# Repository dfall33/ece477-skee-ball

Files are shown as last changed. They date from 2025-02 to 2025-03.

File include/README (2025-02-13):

This directory is intended for project header files.

A header file is a file containing C declarations and macro definitions
to be shared between several project source files. You request the use of a
header file in your project source file (C, C++, etc) located in `src` folder
by including it, with the C preprocessing directive `#include'.

```src/main.c

#include "header.h"

int main (void)
{
 ...
}
```

Including a header file produces the same results as copying the header file
into each source file that needs it. Such copying would be time-consuming
and error-prone. With a header file, the related declarations appear
in only one place. If they need to be changed, they can be changed in one
place, and programs that include the header file will automatically use the
new version when next recompiled. The header file eliminates the labor of
finding and changing all the copies as well as the risk that a failure to
find one copy will result in inconsistencies within a program.

In C, the usual convention is to give header files names that end with `.h'.
It is most portable to use only letters, digits, dashes, and underscores in
header file names, and at most one dot.

Read more about using header files in official GCC documentation:

* Include Syntax
* Include Operation
* Once-Only Headers
* Computed Includes

https://gcc.gnu.org/onlinedocs/cpp/Header-Files.html

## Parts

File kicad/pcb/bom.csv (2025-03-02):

Reference | Value | Datasheet | Footprint | Qty | DNP
C1 | 10nF | ~ | Capacitor_SMD:C_0805_2012Metric_Pad1.18x1.45mm_HandSolder | 1
C3,C6,C10,C12,C14,C16 | 100nF | ~ | Capacitor_SMD:C_0805_2012Metric_Pad1.18x1.45mm_HandSolder | 6
C2 | 1uF | ~ | Capacitor_SMD:C_0805_2012Metric_Pad1.18x1.45mm_HandSolder | 1
C11,C17 | 4.7uF | ~ | Capacitor_SMD:C_0805_2012Metric_Pad1.18x1.45mm_HandSolder | 2
C7 | 10uF | ~ | Capacitor_SMD:C_0805_2012Metric_Pad1.18x1.45mm_HandSolder | 1
R3,R4,R5,R6,R7,R8,R11 | 150 | ~ | Resistor_SMD:R_0805_2012Metric_Pad1.20x1.40mm_HandSolder | 7
R9 | 200 | ~ | Resistor_SMD:R_0805_2012Metric_Pad1.20x1.40mm_HandSolder | 1
R10 | 300 | ~ | Resistor_SMD:R_0805_2012Metric_Pad1.20x1.40mm_HandSolder | 1
R1,R2 | 10k | ~ | Resistor_SMD:R_0805_2012Metric_Pad1.20x1.40mm_HandSolder | 2
RV1 | 10k | ~ | Potentiometer_THT:Potentiometer_Bourns_3339P_Vertical | 1
U5,U6 | 74HC595 | http://www.ti.com/lit/ds/symlink/sn74hc595.pdf | 74HC595N:SOT38-4_NXP | 2
U7 | 74LS08 | http://www.ti.com/lit/gpn/sn74LS08 | SN74LS08N:N14 | 1
J4 | Barrel_Jack | ~ | Connector_BarrelJack:BarrelJack_CUI_PJ-063AH_Horizontal | 1
J5 | Conn_01x05 | ~ | Connector_PinHeader_2.54mm:PinHeader_1x05_P2.54mm_Vertical | 1
J3 | Conn_02x06_Counter_Clockwise | ~ | Connector_PinHeader_2.54mm:PinHeader_2x06_P2.54mm_Vertical | 1
U3 | D24V22F5 | https://engineering.purdue.edu/477grp1/Files/refs/d24v22f5.pdf | 12V_2.2A_STEP-DOWN_D24V22F12:XDCR_12V_2.2A_STEP-DOWN_D24V22F12 | 1
U1 | D24V22F6 | https://engineering.purdue.edu/477grp1/Files/refs/d24v22f6.pdf | 12V_2.2A_STEP-DOWN_D24V22F12:XDCR_12V_2.2A_STEP-DOWN_D24V22F12 | 1
J18 | DC_DRIVER | ~ | Connector_PinHeader_2.54mm:PinHeader_1x02_P2.54mm_Vertical | 1
J2 | EXTERNAL_BUTTON | ~ | Connector_PinHeader_2.54mm:PinHeader_1x02_P2.54mm_Vertical | 1
FB1 | FerriteBead | ~ | Capacitor_SMD:C_0805_2012Metric_Pad1.18x1.45mm_HandSolder | 1
J13 | HEADER | ~ | Connector_PinHeader_2.54mm:PinHeader_1x03_P2.54mm_Vertical | 1
J19 | JOYSTICK | ~ | Connector_PinHeader_2.54mm:PinHeader_1x03_P2.54mm_Vertical | 1
U13 | LD1117S33TR_SOT223 | http://www.st.com/st-web-ui/static/active/en/resource/technical/document/datasheet/CD00000544.pdf | Package_TO_SOT_SMD:SOT-223-3_TabPin2 | 1
D1,D2,D3,D4,D5,D6,D7,D8,D9 | LED | ~ | LED_SMD:LED_0805_2012Metric_Pad1.15x1.40mm_HandSolder | 9
U2 | MAX98357A | https://www.analog.com/media/en/technical-documentation/data-sheets/MAX98357A-MAX98357B.pdf | max98357A:MAX98347A_ADAFRUIT_I2S_BREAKOUT | 1
J20 | SERVO | ~ | Connector_PinHeader_2.54mm:PinHeader_1x03_P2.54mm_Vertical | 1
U4 | STM32F091RCTx | https://engineering.purdue.edu/477grp1/Files/refs/stm32f091cc.pdf | Package_QFP:LQFP-64_10x10mm_P0.5mm | 1
SW1 | SW_Push | ~ | Button_Switch_THT:SW_PUSH_6mm | 1
J21 | US0 | ~ | Connector_PinHeader_2.54mm:PinHeader_1x04_P2.54mm_Vertical | 1
J22 | US1 | ~ | Connector_PinHeader_2.54mm:PinHeader_1x04_P2.54mm_Vertical | 1
J26 | US2 | ~ | Connector_PinHeader_2.54mm:PinHeader_1x04_P2.54mm_Vertical | 1
J27 | US3 | ~ | Connector_PinHeader_2.54mm:PinHeader_1x04_P2.54mm_Vertical | 1
J36 | US4 | ~ | Connector_PinHeader_2.54mm:PinHeader_1x04_P2.54mm_Vertical | 1
U8,U9,U10 | ~ |  | Package_DIP:DIP-12_W10.16mm | 3

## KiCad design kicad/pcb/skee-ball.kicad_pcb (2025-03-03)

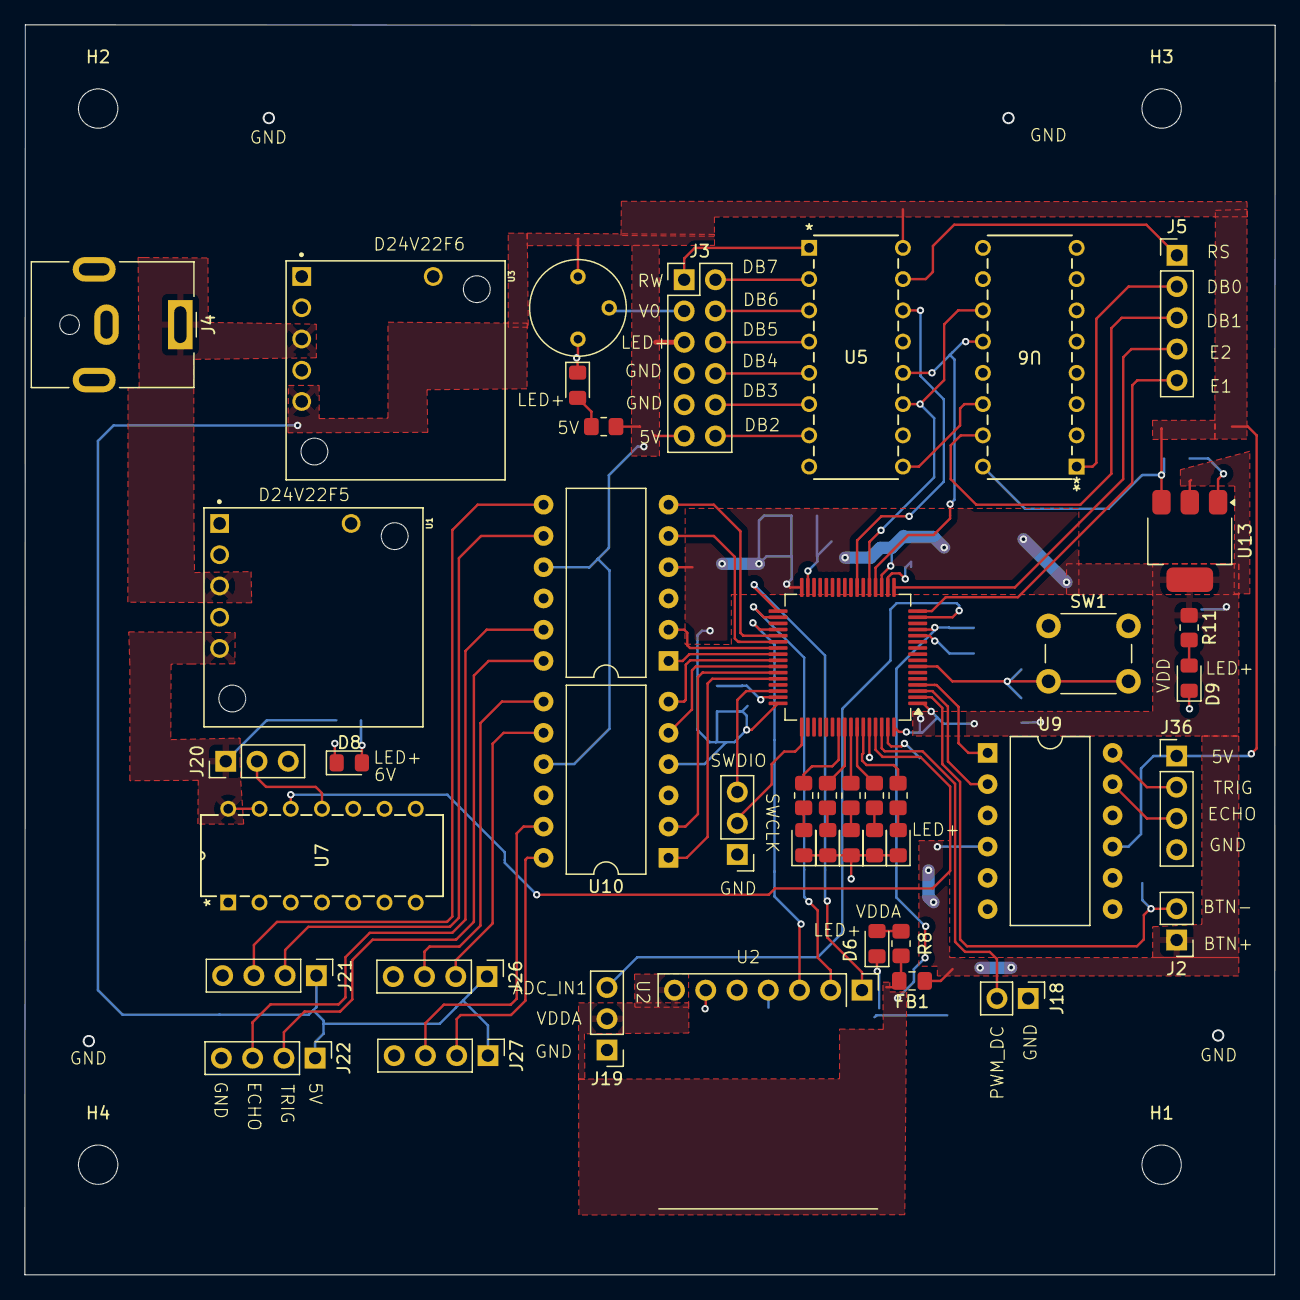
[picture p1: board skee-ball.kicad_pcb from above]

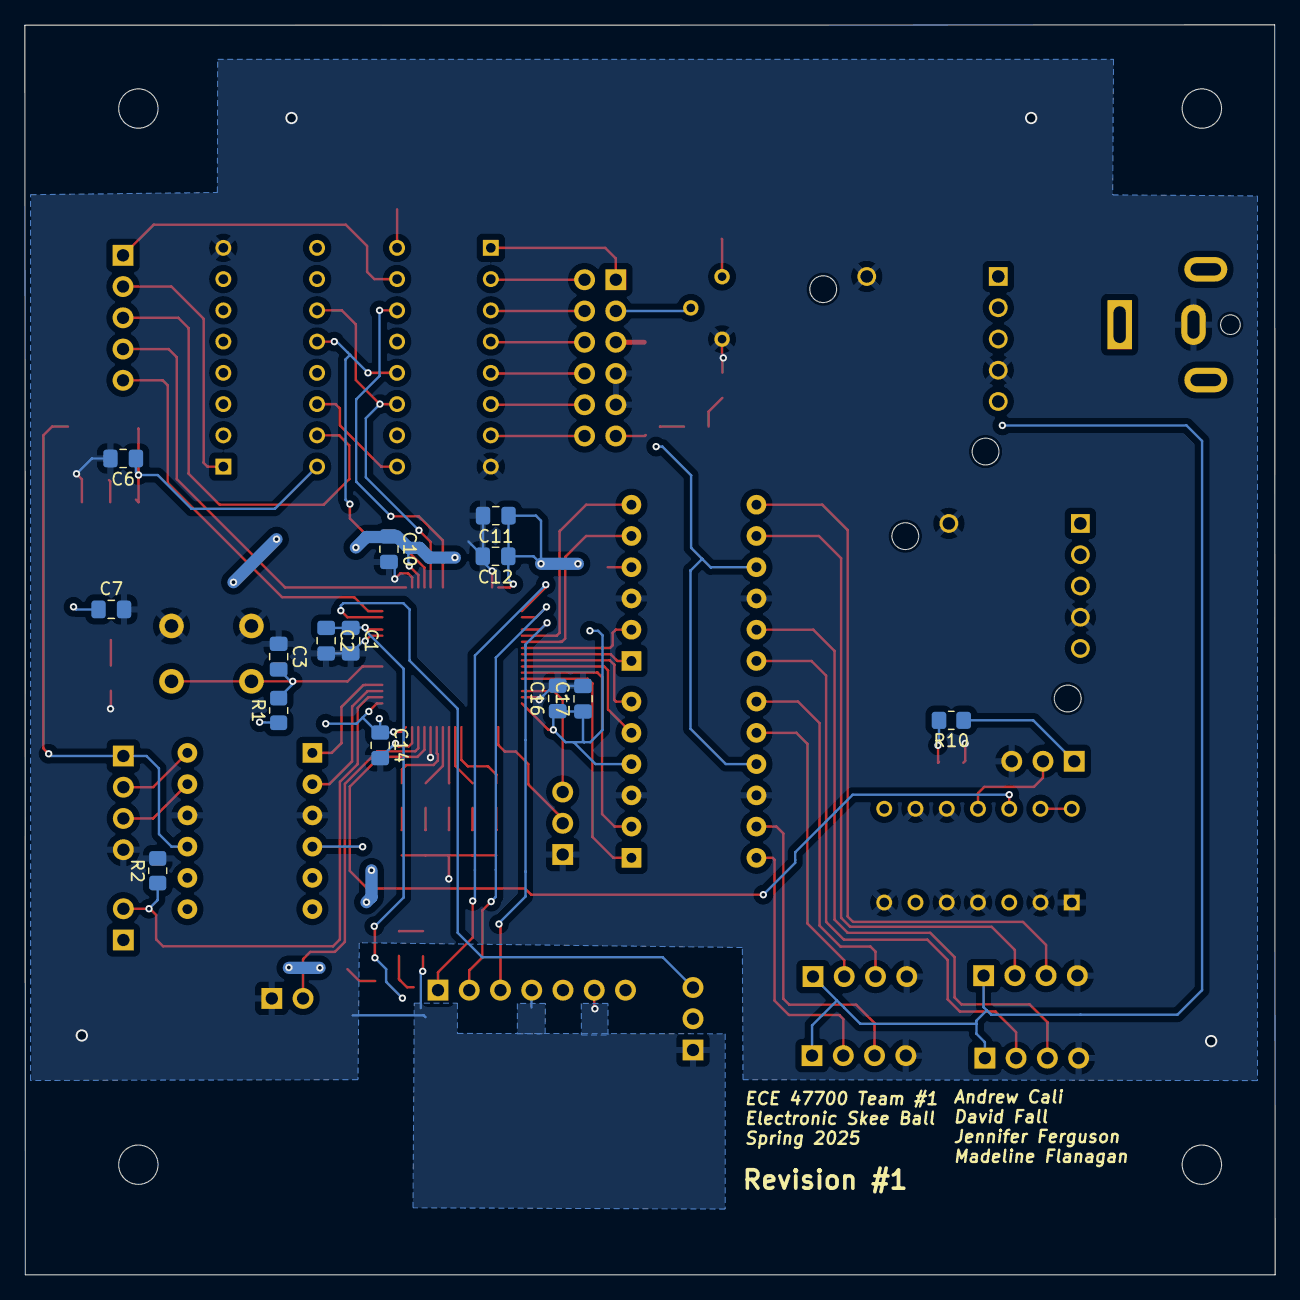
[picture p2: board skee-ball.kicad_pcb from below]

Board: 2 copper layers, 101.6 x 101.6 mm, 62 parts (14 on the bottom side), 68 nets.

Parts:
C1: 10nF; C_0805_2012Metric_Pad1.18x1.45mm_HandSolder
C2: 1uF; C_0805_2012Metric_Pad1.18x1.45mm_HandSolder
C3, C6, C10, C12, C14, C16: 100nF; C_0805_2012Metric_Pad1.18x1.45mm_HandSolder
C7: 10uF; C_0805_2012Metric_Pad1.18x1.45mm_HandSolder
C11, C17: 4.7uF; C_0805_2012Metric_Pad1.18x1.45mm_HandSolder
D1, D2, D3, D4, D5, D6, D7, D8, D9: LED; LED_0805_2012Metric_Pad1.15x1.40mm_HandSolder
FB1: FerriteBead; C_0805_2012Metric_Pad1.18x1.45mm_HandSolder
H1, H2, H3, H4: MountingHole; MountingHole_3.2mm_M3
J2: EXTERNAL_BUTTON; PinHeader_1x02_P2.54mm_Vertical
J3: OLED_CONN1; PinHeader_2x06_P2.54mm_Vertical
J4: Barrel_Jack; BarrelJack_CUI_PJ-063AH_Horizontal
J5: OLED_CONN2; PinHeader_1x05_P2.54mm_Vertical
J13: HEADER; PinHeader_1x03_P2.54mm_Vertical
J18: DC_DRIVER; PinHeader_1x02_P2.54mm_Vertical
J19: JOYSTICK; PinHeader_1x03_P2.54mm_Vertical
J20: SERVO; PinHeader_1x03_P2.54mm_Vertical
J21: US0; PinHeader_1x04_P2.54mm_Vertical
J22: US1; PinHeader_1x04_P2.54mm_Vertical
J26: US2; PinHeader_1x04_P2.54mm_Vertical
J27: US3; PinHeader_1x04_P2.54mm_Vertical
J36: US4; PinHeader_1x04_P2.54mm_Vertical
R1, R2: 10k; R_0805_2012Metric_Pad1.20x1.40mm_HandSolder
R3, R4, R5, R6, R7, R8, R11: 150; R_0805_2012Metric_Pad1.20x1.40mm_HandSolder
R9: 200; R_0805_2012Metric_Pad1.20x1.40mm_HandSolder
R10: 300; R_0805_2012Metric_Pad1.20x1.40mm_HandSolder
RV1: 10k; Potentiometer_Bourns_3339P_Vertical
SW1: SW_Push; SW_PUSH_6mm
U1: D24V22F6; XDCR_12V_2.2A_STEP-DOWN_D24V22F12
U2: MAX98357A; MAX98347A_ADAFRUIT_I2S_BREAKOUT
U3: D24V22F5; XDCR_12V_2.2A_STEP-DOWN_D24V22F12
U4: STM32F091RCTx; LQFP-64_10x10mm_P0.5mm
U5, U6: 74HC595; SOT38-4_NXP
U7: 74LS08; N14
U8, U9, U10: DIP-12_W10.16mm
U13: LD1117S33TR_SOT223; SOT-223-3_TabPin2

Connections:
+5V: C6.1, J3.5, J3.11, J21.1, J22.1, J26.1, J27.1, J36.1, R9.1, RV1.1, U3.5 (VOUT), U5.16 (VCC), U6.16 (VCC), U8.9 (HV), U9.9 (HV), U10.9 (HV), U13.3 (VI)
+6V: J20.1, R10.1, U1.5 (VOUT), U7.13, U7.14 (VCC)
+24V: J4.1, U1.3 (VIN), U3.3 (VIN)
ADC_IN1: J19.3, U4.15 (PA1)
BUTTON_IN: J2.2, R2.1, U4.2 (PC13)
GND: C1.2, C2.2, C3.1, C6.2, C7.2, C10.2, C11.2, C12.2, C14.2, C16.2, C17.2, D1.1 (K), D2.1 (K), D3.1 (K), D4.1 (K), D5.1 (K), D6.1 (K), D7.1 (K), D8.1 (K), D9.1 (K), J3.7, J3.9, J4.2, J13.1, J18.1, J19.1, J20.3, J21.4, J22.4, J26.4, J27.4, J36.4, R2.2, RV1.3, SW1.1, U1.4 (GND), U1.6 (GND), U2.4 (GAIN), U2.6 (GND), U3.4 (GND), U3.6 (GND), U4.12 (VSSA), U4.18 (VSS), U4.31 (VSS), U4.47 (VSS), U4.60 (PF11), U4.63 (VSS), U5.8 (GND), U6.8 (GND), U7.1, U7.2, U7.4, U7.5, U7.7 (GND), U7.9, U7.10, U8.3 (GND), U8.10 (GND), U9.3 (GND), U9.10 (GND), U10.3 (GND), U10.10 (GND), U13.1 (GND)
NHD_DB0: J5.2, U6.1 (QB)
NHD_DB1: J5.3, U6.15 (QA)
NHD_DB2: J3.12, U5.7 (QH)
NHD_DB3: J3.10, U5.6 (QG)
NHD_DB4: J3.8, U5.5 (QF)
NHD_DB5: J3.6, U5.4 (QE)
NHD_DB6: J3.4, U5.3 (QD)
NHD_DB7: J3.2, U5.2 (QC)
NHD_E1: J5.5, U4.16 (PA2)
NHD_E2: J5.4, U4.17 (PA3)
NHD_RS: J5.1, U5.15 (QA)
NHD_RW: J3.1, U5.1 (QB)
NHD_V0: J3.3, RV1.2
NRST: C3.2, R1.2, SW1.2, U4.7 (NRST)
unnamed: D1.2 (A), R3.2
unnamed: D2.2 (A), R4.2
unnamed: D3.2 (A), R5.2
unnamed: D4.2 (A), R6.2
unnamed: D5.2 (A), R7.2
unnamed: D6.2 (A), R8.2
unnamed: D7.2 (A), R9.2
unnamed: D8.2 (A), R10.2
unnamed: D9.2 (A), R11.2
PB3: R6.1, U4.55 (PB3)
PB4: R7.1, U4.56 (PB4)
PB5: R3.1, U4.57 (PB5)
PB6: R4.1, U4.58 (PB6)
PB7: R5.1, U4.59 (PB7)
PWM_DC: J18.2, U4.62 (PB9)
PWM_SERVO_3.3: U4.61 (PB8), U7.12
PWM_SERVO_6: J20.2, U7.11
RCLK: U4.20 (PA4), U5.12 (RCLK), U6.12 (RCLK)
SER-CHAIN: U5.9 (QH'), U6.14 (SER)
SPI1-MOSI: U4.23 (PA7), U5.14 (SER)
SPI1-SCK: U4.21 (PA5), U5.11 (SRCLK), U6.11 (SRCLK)
SPI2-MOSI(I2S_SD): U2.3 (DIN), U4.36 (PB15)
SPI2-NSS(I2S_WS): U2.1 (LRCLK), U4.33 (PB12)
SPI2-SCK(I2S_CK): U2.2 (BCLK), U4.34 (PB13)
SWCLK: J13.2, U4.49 (PA14)
SWDIO: J13.3, U4.46 (PA13)
US_ECHO0_3.3: U4.37 (PC6), U8.6 (LV1)
US_ECHO0_5: J21.3, U8.7 (HV1)
US_ECHO1_3.3: U4.39 (PC8), U8.2 (LV3)
US_ECHO1_5: J22.3, U8.11 (HV3)
US_ECHO2_3.3: U4.41 (PA8), U10.6 (LV1)
US_ECHO2_5: J26.3, U10.7 (HV1)
US_ECHO3_3.3: U4.43 (PA10), U10.2 (LV3)
US_ECHO3_5: J27.3, U10.11 (HV3)
US_ECHO4_3.3: U4.3 (PC14), U9.2 (LV3)
US_ECHO4_5: J36.3, U9.11 (HV3)
US_TRIG0_3.3: U4.38 (PC7), U8.5 (LV2)
US_TRIG0_5: J21.2, U8.8 (HV2)
US_TRIG1_3.3: U4.40 (PC9), U8.1 (LV4)
US_TRIG1_5: J22.2, U8.12 (HV4)
US_TRIG2_3.3: U4.42 (PA9), U10.5 (LV2)
US_TRIG2_5: J26.2, U10.8 (HV2)
US_TRIG3_3.3: U4.44 (PA11), U10.1 (LV4)
US_TRIG3_5: J27.2, U10.12 (HV4)
US_TRIG4_3.3: U4.4 (PC15), U9.1 (LV4)
US_TRIG4_5: J36.2, U9.12 (HV4)
VDD: C7.1, C10.1, C11.1, C12.1, C14.1, C16.1, C17.1, FB1.1, J2.1, R1.1, R11.1, U4.1 (VBAT), U4.19 (VDD), U4.32 (VDD), U4.48 (VDDIO2), U4.64 (VDD), U8.4 (LV), U9.4 (LV), U10.4 (LV), U13.2 (VO)
VDDA: C1.1, C2.1, FB1.2, J19.2, R8.1, U2.7 (VDD), U4.13 (VDDA)

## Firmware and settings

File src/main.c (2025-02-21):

#include "stm32f0xx.h"
#include <math.h> // for M_PI
#include <stdint.h>
#include <stdio.h>
#include "ultrasonic.h"
#include "button.h"
#include "nhd_0440az.h"

#define PULSE_TIMEOUT_US 30000
#define PULSE_THRESHOLD_US 200

volatile int detected_streak = 0;

/* ----- Function Declarations ----- */
void nano_wait(int);
void micro_wait(int);

void init_exti();
void init_gpio();

void spi1_init_oled();
void spi1_display1(const char *);
void spi1_display2(const char *);
void spi_cmd(unsigned int);
void spi_clear();
void spi_data(unsigned int);
void init_spi1();

void setup_tim3();
void setup_tim14();
void setup_tim15();

void init_gpio()
{

    // =======================================================
    /* ----- Configure Port A ----- */
    // =======================================================
    RCC->AHBENR |= RCC_AHBENR_GPIOAEN;
    /* ----- Configure PA4 as Output for RCLK ----- */
    GPIOA->MODER &= ~(GPIO_MODER_MODER4);
    GPIOA->MODER |= GPIO_MODER_MODER4_0; // Output mode

    /* ----- Configure PA2 and PA3 as NHD E1 and NHD E2, respectively ----- */
    GPIOA->MODER &= ~(GPIO_MODER_MODER2 | GPIO_MODER_MODER3);
    GPIOA->MODER |= GPIO_MODER_MODER2_0 | GPIO_MODER_MODER3_0; // Output mode

    // =======================================================
    /* ----- Configure Port C ----- */
    // =======================================================

    RCC->AHBENR |= RCC_AHBENR_GPIOCEN;

    /* ----- Configure PC0 for Push Button */
    GPIOC->MODER &= ~(GPIO_MODER_MODER0);

    /* ----- Configure PC1-PC10 for ultrasonic sensors -----  */
    // Configure PC1 as input with internal pull-down
    GPIOC->MODER &= ~(GPIO_MODER_MODER1);
    GPIOC->PUPDR &= ~(GPIO_PUPDR_PUPDR1);

    // Configure PC2 as input with internal pull-down
    GPIOC->MODER &= ~(GPIO_MODER_MODER2);
    GPIOC->PUPDR &= ~(GPIO_PUPDR_PUPDR2);

    // Configure PC3 as input with internal pull-down
    GPIOC->MODER &= ~(GPIO_MODER_MODER3);
    GPIOC->PUPDR &= ~(GPIO_PUPDR_PUPDR3);

    // Configure PC4 as input with internal pull-down
    GPIOC->MODER &= ~(GPIO_MODER_MODER4);
    GPIOC->PUPDR &= ~(GPIO_PUPDR_PUPDR4);

    // Configure PC5 as input with internal pull-down
    GPIOC->MODER &= ~(GPIO_MODER_MODER5);
    GPIOC->PUPDR &= ~(GPIO_PUPDR_PUPDR5);

    // Configure PC6 as output
    GPIOC->MODER &= ~(GPIO_MODER_MODER6);
    GPIOC->MODER |= GPIO_MODER_MODER6_0; // Output mode

    // Configure PC7 as output
    GPIOC->MODER &= ~(GPIO_MODER_MODER7);
    GPIOC->MODER |= GPIO_MODER_MODER7_0; // Output mode

    // Configure PC8 as output
    GPIOC->MODER &= ~(GPIO_MODER_MODER8);
    GPIOC->MODER |= GPIO_MODER_MODER8_0; // Output mode

    // Configure PC9 as output
    GPIOC->MODER &= ~(GPIO_MODER_MODER9);
    GPIOC->MODER |= GPIO_MODER_MODER9_0; // Output mode

    // Configure PC10 as output
    GPIOC->MODER &= ~(GPIO_MODER_MODER10);
    GPIOC->MODER |= GPIO_MODER_MODER10_0; // Output mode
}

void init_exti()
{
    // enable SYSCFG clock
    RCC->APB2ENR |= RCC_APB2ENR_SYSCFGEN;

    // set PC0 as external interrupt source
    SYSCFG->EXTICR[0] &= ~SYSCFG_EXTICR1_EXTI0;
    SYSCFG->EXTICR[0] |= SYSCFG_EXTICR1_EXTI0_PC;

    // enable interrupt on rising edge and falling edge
    EXTI->RTSR |= EXTI_RTSR_TR0;
    EXTI->FTSR |= EXTI_FTSR_TR0;

    // enable interrupt on line 0
    EXTI->IMR |= EXTI_IMR_MR0;

    // don't enable the interrupt until the game has started / button can be pressed
    NVIC_EnableIRQ(EXTI0_1_IRQn);
}

/* ----- External Interrupt Handler for PC ----- */
void EXTI0_1_IRQHandler(void)
{
    EXTI->PR |= EXTI_PR_PR0;
    if (GPIOC->IDR & GPIO_IDR_0)
    {
        start_button_press();
    }
    else
    {
        stop_button_press();
    }
}

/* ----- This timer is used for timing out individual ultrasonic sensor readings ----- */
void setup_tim14()
{

    // enable clock to TIM14
    RCC->APB1ENR |= RCC_APB1ENR_TIM14EN;

    // TIM14->ARR = 1440000;
    TIM14->PSC = 48 - 1; // 48 MHz / 48 = 1 MHz
    TIM14->ARR = 30000;  // 1 MHz / 30000 = 33.33 Hz

    // enable the interrupt on timer overflow
    TIM14->DIER |= TIM_DIER_UIE;

    // enable the interrupt in the NVIC
    NVIC_EnableIRQ(TIM14_IRQn);

    // enable the timer
    // TIM14->CR1 |= TIM_CR1_CEN;

    // don't enable the timer yet, because we want to start it when we start the ultrasonic sensor
}

/* ----- This timer is used for timing out the ultrasonic search overall, i.e., search for the ball for N seconds then give up ----- */
void setup_tim15()
{
    RCC->APB2ENR |= RCC_APB2ENR_TIM15EN;
    TIM15->PSC = 48 - 1;                   // 48 MHz / 48 = 1 MHz
    TIM15->ARR = HCSR04_SEARCH_TIMEOUT_US; // 1 MHz / 10000 = 100 Hz

    TIM15->DIER |= TIM_DIER_UIE;
    NVIC_EnableIRQ(TIM15_IRQn);
}

void setup_tim3()
{
    RCC->APB1ENR |= RCC_APB1ENR_TIM3EN;
    TIM3->PSC = 48000 - 1; // 48 MHz / 48000 = 1 kHz
    TIM3->ARR = BUTTON_MAX_PRESS_US;
    TIM3->CNT = 0;
    TIM3->DIER |= TIM_DIER_UIE;
    NVIC_EnableIRQ(TIM3_IRQn);

    // don't enable the timer until we are ready to accept button presses (depends on game state)
}

void TIM3_IRQHandler(void)
{
    TIM3->SR &= ~TIM_SR_UIF;
    time_out_button();
}

void TIM14_IRQHandler(void)
{
    TIM14->SR &= ~TIM_SR_UIF;
    time_out_pulse();
}

void TIM15_IRQHandler(void)
{
    TIM15->SR &= ~TIM_SR_UIF;
    time_out_hcsr04_search();
}

void init_spi1()
{
    // enable clock for SPI1
    RCC->APB2ENR |= RCC_APB2ENR_SPI1EN;

    RCC->AHBENR |= RCC_AHBENR_GPIOAEN;
    GPIOA->MODER &= ~(GPIO_MODER_MODER15 | GPIO_MODER_MODER5 | GPIO_MODER_MODER7);
    GPIOA->MODER |= GPIO_MODER_MODER15_1 | GPIO_MODER_MODER5_1 | GPIO_MODER_MODER7_1;

    // set the alternate function for the pins (SCK, MOSI, NSS are all alternate function 0)

    // reset the alternate function bits for the pins
    GPIOA->AFR[0] &= ~(GPIO_AFRL_AFRL7 | GPIO_AFRL_AFRL5);
    GPIOA->AFR[1] &= ~(GPIO_AFRH_AFRH7);

    // configure NSS, SCK, MOSI signals of SPI1 to pins PA15, PA5, PA7, respectively
    // set the alternate function bits for the pins
    GPIOA->AFR[0] |= (0x0 << GPIO_AFRL_AFRL7_Pos) | (0x0 << GPIO_AFRL_AFRL5_Pos);
    GPIOA->AFR[1] |= (0x0 << GPIO_AFRH_AFRH7_Pos);

    // disable SPI1
    SPI1->CR1 &= ~SPI_CR1_SPE;

    // set baud rate to max possible
    SPI1->CR1 |= SPI_CR1_BR;

    // configure for 16-bit word size
    SPI1->CR2 |= SPI_CR2_DS;
    // SPI1->CR2 &= ~(SPI_CR2_DS_2 | SPI_CR2_DS_1);

    // configure the SPI channel to be in master configuration
    SPI1->CR1 |= SPI_CR1_MSTR;

    // set the SS ouptut enable pit and enable NSSP
    SPI1->CR2 |= SPI_CR2_SSOE;
    SPI1->CR2 |= SPI_CR2_NSSP;

    // set the TXDMAEN to enable DMA transfers on transmit buffer empty
    SPI1->CR2 |= SPI_CR2_TXDMAEN;

    // enable the SPI channel
    SPI1->CR1 |= SPI_CR1_SPE;
}

void spi_cmd(unsigned int data)
{
    // wait until spi1 TX is empty
    while ((SPI1->SR & SPI_SR_TXE) == 0)
        ;

    // copy data to spi1 data register
    SPI1->DR = data;
}
void spi_data(unsigned int data)
{
    // call spi_cmd with (data | 0x200)
    unsigned int val = data | 0x200;
    spi_cmd(val);
}
void spi1_init_oled()
{
    int millisecond = 1000000;
    // wait 1ms with nano_wait
    nano_wait(millisecond);

    // call spi_cmd with 0x38 to do a function set
    spi_cmd(0x38);

    // call spi_cmd with 0x08 to turn off the display
    spi_cmd(0x08);

    // call spi_cmd with 0x01 to clear the display
    spi_cmd(0x01);

    // wait 2ms using nano_wait
    nano_wait(2 * millisecond);

    // call spi_cmd with 0x06 to set the entry mode
    spi_cmd(0x06);

    // call spi_cmd with 0x02 to move the cursor to the home position
    spi_cmd(0x02);

    // call spi_cmd with 0x0c to turn on the display
    spi_cmd(0x0c);
}
void spi1_display1(const char *string)
{
    // move the cursor to the home position
    spi_cmd(0x02);

    // for each character in the string
    // call spi_data with the character

    // iterate over the string using string++
    while (*string != '\0')
    {
        spi_data(*string);
        string++;
    }
}

void spi_clear()
{
    // move the cursor to the home position
    spi_cmd(0x02);

    // iterate over the string using string++
    for (int i = 0; i < 16; i++)
    {
        spi_data(' ');
    }

    // clear the second row
    spi_cmd(0xc0);
    for (int i = 0; i < 16; i++)
    {
        spi_data(' ');
    }
}

void spi1_display2(const char *string)
{
    // move the cursor to the second row
    spi_cmd(0xc0);

    // for each character in the string
    // call spi_data with the character

    // iterate until null terminator
    while (*string != '\0')
    {
        spi_data(*string);
        string++;
    }
}

int main(void)
{
    internal_clock();
    init_gpio();
    setup_tim3();
    setup_tim14();
    init_spi1();
    spi1_init_oled();
    init_exti();

    init_display();
    spi_write_str("Line 1, abc", 0);
    spi_write_str("Line 2, def", 1);
    spi_write_str("Line 3, ghi", 2);
    spi_write_str("Line 4, jkl", 3);

    return 0;

    uint16_t flash_val = 0x0200;
    load_shift_registers(0x0000);
    micro_wait(1000000);
    load_shift_registers(flash_val);
    micro_wait(1000000);

    load_shift_registers(0x0000);
    micro_wait(1000000);
    load_shift_registers(flash_val);
    micro_wait(1000000);

    load_shift_registers(0x0000);
    micro_wait(1000000);
    load_shift_registers(flash_val);
    micro_wait(1000000);

    load_shift_registers(0x0000);
    micro_wait(1000000);
    load_shift_registers(flash_val);
    micro_wait(1000000);
}

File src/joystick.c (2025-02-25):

#include "stm32f0xx.h"
#include <stdio.h>

// Servo Parameters
#define SERVO_MIN_PULSE  500   // 500us
#define SERVO_MAX_PULSE  2500  // 2500us
#define PWM_PERIOD       3325  // Corresponding to 50Hz (20ms) with 48MHz clock

volatile int degrees = 45;
volatile int adc = 0;
void setup_adc(void);
void setup_tim16(void);
void init_tim2(void);
void move_to_angle(int angle);
int read_joystick(void);
int map_adc_to_degrees(int adc_val);

//Setup ADC for Joystick Input (PA1)
void setup_adc(void) {
    RCC->AHBENR |= RCC_AHBENR_GPIOAEN;  
    GPIOA->MODER |= 0xC;                
    RCC->APB2ENR |= RCC_APB2ENR_ADCEN;  
    RCC->CR2 |= RCC_CR2_HSI14ON;        
    while (!(RCC->CR2 & RCC_CR2_HSI14RDY));
    ADC1->CR |= ADC_CR_ADEN;            
    while (!(ADC1->ISR & ADC_ISR_ADRDY));
    ADC1->CHSELR |= ADC_CHSELR_CHSEL1;
    while (!(ADC1->ISR & ADC_ISR_ADRDY));
}

//Setup PWM on TIM16 Channel 1 (PB8)
void setup_tim16(void) {   

    RCC->AHBENR |= RCC_AHBENR_GPIOBEN;    
    RCC->APB2ENR |= RCC_APB2ENR_TIM16EN;  

    GPIOB->MODER &= ~0x00030000;  
    GPIOB->MODER |= GPIO_MODER_MODER8_1;  
    GPIOB->AFR[1] &= ~0x0000000F; 
    GPIOB->AFR[1] |= 0x2;         

    TIM16->PSC = 16 - 1;                 
    TIM16->ARR = 60000 - 1;         
    TIM16->BDTR |= TIM_BDTR_MOE;
    // PWM Mode 1 on CH1
    TIM16->CCMR1 &= ~TIM_CCMR1_OC1M;
    TIM16->CCMR1 |= (6 << TIM_CCMR1_OC1M_Pos);  // PWM mode 1
    TIM16->CCMR1 |= TIM_CCMR1_OC1PE;         

    // Set duty cycle
    // TIM16->CCR1 = 1500;

    TIM16->CCER |= TIM_CCER_CC1E;
    TIM16->EGR |= TIM_EGR_UG;
    TIM16->CR1 |= TIM_CR1_CEN;
    move_to_angle(degrees);    
}


//Convert ADC Value to Degree
int map_adc_to_degrees(int adc_val) {
    int adc_min = 0, adc_max = 4095;
    int deg_min = -4, deg_max = 4;
    int val = ((adc_val - adc_min) * (deg_max - deg_min) / (adc_max - adc_min)) + deg_min;
    if (adc_val <= 2100 && adc_val >= 1900) val = 0;
    return val;
}

//Move Servo to Specified Angle
void move_to_angle(int angle) {
    if (angle < 0) angle = 0;
    if (angle > 180) angle = 180;

    int pulse_width = SERVO_MIN_PULSE + ((angle * (SERVO_MAX_PULSE - SERVO_MIN_PULSE)) / 180);
    TIM16->CCR1 = pulse_width;  // Set duty cycle
    printf("Moving to %d degrees (Pulse: %d)\n", angle, pulse_width);
}

//Read Joystick ADC Value
int read_joystick(void) {
    ADC1->CR |= ADC_CR_ADSTART;          
    while (!(ADC1->ISR & ADC_ISR_EOC));  
    return ADC1->DR;                     
}

//Timer 2 ISR
void TIM2_IRQHandler() {
    TIM2->SR &= ~TIM_SR_UIF;
    ADC1->CR |= ADC_CR_ADSTART;
    while(!(ADC1->ISR & ADC_ISR_EOC));
    
    int adc_val = ADC1->DR;
    adc = adc_val;
    int inc_degrees = map_adc_to_degrees(adc_val);
    
    if ((degrees + inc_degrees) >= 0 && (degrees + inc_degrees) <= 180) {
        degrees += inc_degrees;
    }

    move_to_angle(degrees);
    }

//Setup TIM15 for Periodic Joystick Reading
void init_tim2(void) {

    RCC->APB1ENR |= RCC_APB1ENR_TIM2EN;
    TIM2->PSC = 480 -1;
    TIM2->ARR = 1000 -1;
    TIM2->DIER |= TIM_DIER_UIE;
    NVIC->ISER[0] = 1<< TIM2_IRQn;
    TIM2->CR1 |= TIM_CR1_CEN;
}

int main(void) {
    RCC->AHBENR |= RCC_AHBENR_GPIOCEN;
  GPIOC->MODER &= ~0x000000ff; //inputs
  GPIOC->PUPDR |=  0x000000aa;
  GPIOC->MODER |=  0x00005500; //outputs
    setup_adc();
    setup_tim16();
    init_tim2();
    GPIOC->ODR = 1 << (8-1);
    while (1);
}

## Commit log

2025-01-22 prototype push button press duration
2025-01-23 prototype oled display
2025-01-26 prototype I2S usage
2025-01-29 Create ultrasonic_prototyping.py
    prototype ultrasonic sensor hc-sr04
2025-01-30 test ultrasonic mux
2025-02-16 begin schematic and pcb layout
    [skee-ball.kicad_pcb, skee-ball.kicad_sch]
2025-02-17 add to pcb schematic
    [skee-ball.kicad_pcb, skee-ball.kicad_sch]
2025-02-18 add ultrasonic module
    [skee-ball.kicad_sch]
2025-02-19 added external parts schematic project
    couldn't find symbols for most components, so will need to create custom ones if necessary
    [External-parts.kicad_pcb, External-parts.kicad_sch, Servo-motor.kicad_sch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]
2025-02-19 add AND gate to pcb schematic
    [skee-ball.kicad_sch]
2025-02-19 add ultrasonic, speaker, nhd
    [External-parts.kicad_sch, Servo-motor.kicad_sch, nhd_0440az.kicad_sch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]
2025-02-19 add timer labels to pwm signals
    [skee-ball.kicad_sch]
2025-02-19 add push button module
2025-02-19 fix spi1 mosi pin assignment
    [skee-ball.kicad_sch]
2025-02-20 add LDOs to pcb schematic
    [skee-ball.kicad_sch]
2025-02-20 update cap values for stm supply voltage
    [skee-ball.kicad_sch]
2025-02-21 fix nhd enable signal label on schematic
    [skee-ball.kicad_sch]
2025-02-21 added header connection pins
    [skee-ball.kicad_sch]
2025-02-21 add debugging circuitry to schematic
    [skee-ball.kicad_sch]
2025-02-23 added pcb layout
    [skee-ball.kicad_pcb, skee-ball.kicad_sch]
2025-02-25 begin routing on pcb
    [skee-ball.kicad_pcb, skee-ball.kicad_sch]
2025-02-25 add decoupling circuitry for mcu power
    [skee-ball.kicad_sch]
2025-02-26 added ground plane and some via connections
    [skee-ball.kicad_pcb]
2025-02-26 update pcb
    [skee-ball.kicad_pcb, skee-ball.kicad_sch]
2025-02-27 add level shifter
    [skee-ball.kicad_sch]
2025-02-27 transition to level shifters
    [skee-ball.kicad_pcb, skee-ball.kicad_sch]
2025-02-27 add new connector footprints
    [skee-ball.kicad_pcb, skee-ball.kicad_sch]
2025-02-28 add first successful routing
    [skee-ball.kicad_pcb, skee-ball.kicad_sch]
2025-02-28 finish routing
    [skee-ball.kicad_pcb, skee-ball.kicad_sch]
2025-03-01 added power zones and started debugging DRC
    [skee-ball.kicad_pcb]
2025-03-01 eliminate all drc errors
    [skee-ball.kicad_pcb, skee-ball.kicad_sch]
2025-03-02 finish pcb silkscreen
    [skee-ball.kicad_pcb, skee-ball.kicad_sch]
2025-03-02 generate gerber and bom
    [skee-ball.kicad_sch]
2025-03-02 add gerbers
    [bom.csv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]
2025-03-02 minor changes
    [skee-ball.kicad_pcb]
2025-03-02 remove unneccesary 5v rail
    [skee-ball.kicad_pcb]
2025-03-03 minor changes to schematic
    [skee-ball-B_Cu.gbr, skee-ball-B_Mask.gbr, skee-ball-B_Paste.gbr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]
2025-03-03 reposition pcb mounting holes
    [skee-ball.kicad_pcb]
2025-03-03 update silkscreen
    [skee-ball.kicad_pcb]
